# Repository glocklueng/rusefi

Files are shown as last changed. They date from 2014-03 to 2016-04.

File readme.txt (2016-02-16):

current binaries are always available at http://rusefi.com/build_server/

#Releases

| Release date  | Revision  | Details |
| ---  | --- | --- |
| 02/15/2016	| r9600 | automatic warm-up fuel correction, performance improvements
| 08/31/2015	| r8725 | acceleration fuel correction, console improvements
| 07/06/2015	| r8554 | more CAN, better console, bugfixes, performance
| 04/26/2015	| r7938	 | vehicle speed sensor, stepper idle valve, lots of improvements
| 11/13/2014	| r5327	 | ChibiOS/RT 2.6.6, better cold start logic, bugfixes, bugfixes, bugfixes...
| 06/12/2014	| r3477	 | Precise event scheduling, protocol selection 
| 03/26/2014	| r2413	 | C++, refactoring & improvements
| 02/23/2013	| r1777	 | trigger is now configurable via TunerStudio
| 01/30/2014	| r1309	 | true trigger angles, VBatt signal
| 01/12/2014	| r1007	 | refactoring, refactoring & refactoring
| 12/19/2013	| r605	 | ignition control & a little bit of CAN bus
| 11/08/2013	| r100	 | Tuner Studio fuel map tuning, fuel pump control
| 10/14/2013	| r39	 | USB serial bug, missing IAR files, self-containted Makefile
| 10/13/2013	| r33	 | IAR project file
| 10/04/2013	| r26	 | Patched ChibiOS/RT 2.6.1 sources are now included
| 09/23/2013	| r20	 | Tuner Studio integration, configuraton persistence
| 08/30/2013	| r14	 | initial documentation & refactoring. tunerstudio integration
| 08/03/2013	| r13	 | wideband O2 input, better idling algorithm, serial-over-USB
| 07/05/2013	| r10	 | Second CKP, sequential injection.
| 06/19/2013	| r9	 | Initial version - batch injection & ignition with advance table lookup.

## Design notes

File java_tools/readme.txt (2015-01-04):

Here we have some tiny utilities
gcc_map_reader reads the .map file produced by GCC and prints some details on what is RAM used for
ts2c reads a piece of TunerStudio map and produces a matching C language piece of code
version2header creates a C language header containting current SVN version
enum2string

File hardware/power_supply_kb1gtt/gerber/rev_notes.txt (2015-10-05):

This is a copy of https://code.google.com/p/daecu/source/browse/#svn%2FHardware%2Ftrunk%2FKICAD_Project_PWR_buck_12V_switcher with lib split up per standard rusEFI file practices. 

R0.1 first spin
R0.3 adjusted to be easier to MFG with an iron.
R0.4 Added MOSFET that allows 150V surge protection

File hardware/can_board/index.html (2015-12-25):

forum thread (http://rusefi.com/forum/viewtopic.php?f=4&t=353)
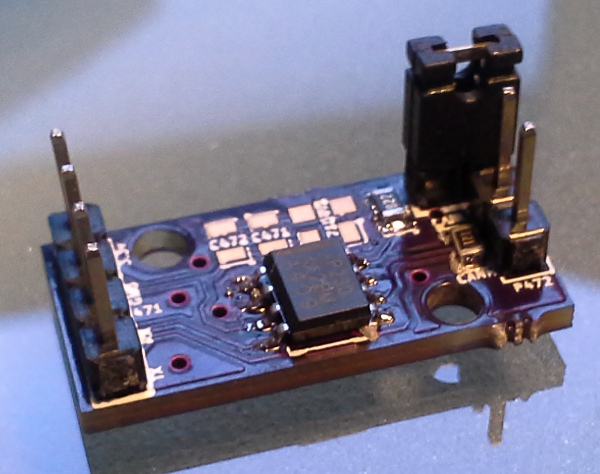
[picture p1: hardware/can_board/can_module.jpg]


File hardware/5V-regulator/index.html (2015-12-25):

forum thread (http://rusefi.com/forum/viewtopic.php?f=4&t=893)
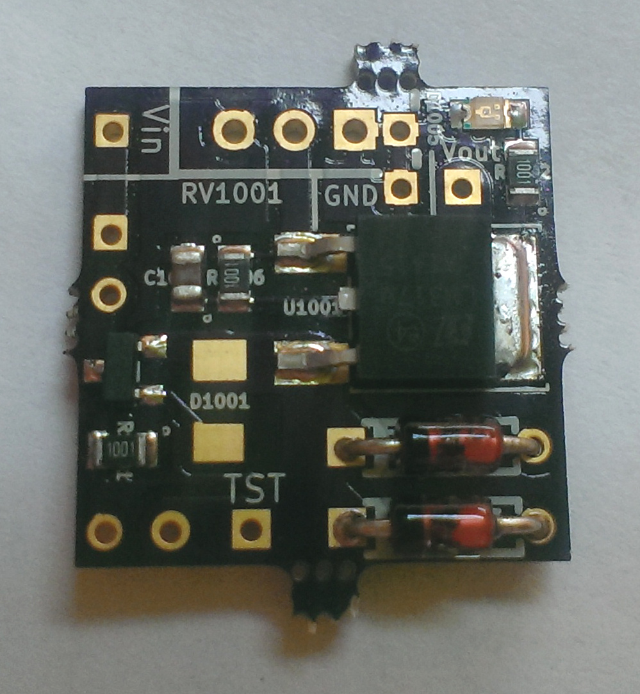
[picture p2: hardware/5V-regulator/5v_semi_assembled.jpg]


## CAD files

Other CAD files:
hardware/mazda_b_case/B3_ECU_PCB.dwg

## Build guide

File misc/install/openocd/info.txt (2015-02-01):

OpenOCD 0.8.0
commit date: 27.04.2014 10:28:21
build date: 28.04.2014
package date: 28.04.2014
build system: Linux 3.14.1-1-ARCH #1 SMP PREEMPT Mon Apr 14 20:40:47 CEST 2014 x86_64 GNU/Linux
compiler: GCC 4.8.2 (i686-w64-mingw32 / x86_64-w64-mingw32; 4.8.2-5 package in Arch Linux)

Libraries used:
hidapi-0.8.0-rc1
libftdi-1.1
libusb-win32-1.2.6.0
libusb-1.0.18

Build commands used for 32-bit version:
../configure --host=i686-w64-mingw32 --prefix= --enable-aice --enable-amtjtagaccel --enable-armjtagew
	--enable-cmsis-dap --enable-ftdi --enable-gw16012 --enable-jlink --enable-jtag_vpi --enable-legacy-ft2232_libftdi
	--enable-opendous --enable-openjtag_ftdi --enable-osbdm --enable-parport --disable-parport-ppdev
	--enable-parport-giveio --enable-presto_libftdi --enable-remote-bitbang --enable-rlink --enable-stlink
	--enable-ti-icdi --enable-ulink --enable-usb-blaster-2 --enable-usb_blaster_libftdi --enable-usbprog
	--enable-vsllink
make bindir="bin" pkgdatadir=
i686-w64-mingw32-strip src/openocd.exe

Build commands used for 64-bit version:
../configure --host=x86_64-w64-mingw32 --prefix= --enable-aice --enable-amtjtagaccel --enable-armjtagew
	--enable-cmsis-dap --enable-ftdi --enable-gw16012 --enable-jlink --enable-jtag_vpi --enable-legacy-ft2232_libftdi
	--enable-opendous --enable-openjtag_ftdi --enable-osbdm --enable-parport --disable-parport-ppdev
	--enable-parport-giveio --enable-presto_libftdi --enable-remote-bitbang --enable-rlink --enable-stlink
	--enable-ti-icdi --enable-ulink --enable-usb-blaster-2 --enable-usb_blaster_libftdi --enable-usbprog
	--enable-vsllink
make bindir="bin-x64" pkgdatadir=
x86_64-w64-mingw32-strip src/openocd.exe

This package and info about it can be found on Freddie Chopin's website:
http://www.freddiechopin.info/

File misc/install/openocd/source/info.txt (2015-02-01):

You can download the source code from sourceforge
http://sourceforge.net/projects/openocd/files/openocd/0.8.0/

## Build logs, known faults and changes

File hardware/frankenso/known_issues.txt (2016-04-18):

 1) RESOLVED IN R0.2  upper mounting hole does not align - see http://rusefi.com/images/Frankenso/frankenso_0_1_back.jpg
 2) RESOLVED IN R0.2  add a jumper to isolate C1002 & C1003 while powered via USB? see http://rusefi.com/forum/viewtopic.php?f=4&t=569&start=50#p9859
 3) RESOLVED IN R0.2  usability issue: GND test pad is under discovery
 4) RESOLVED IN R0.2  add larger +5 test pad?
 5) RESOLVED IN R0.2  add +12 test point?
 6) RESOLVED IN R0.2  Thermocouple needs a via to allow a zip tie to go fully around the connector.
 7) RESOLVED IN R0.2  op-amp reference & part # silkscreen is upside down in relation to the labeling of the actual chips
 8) RESOLVED IN R0.2  Make HIP9011 components into 0805 for common parts
 9) RESOLVED IN R0.2  VDD on STM discovery should be 3V not 5V.  
10) RESOLVED IN R0.2  LCD mounting holes are too small for the Chinese M3 stand-offs
11) RESOLVED IN R0.2  SD card PB4 should be SO not SI PB5 should be SI not SO. 
12) RESOLVED IN R0.2  USB D- and D+ were on wrong pins, D+ now on USB pin 3, TTL RX and TX were also on the wrong pins 
13) RESOLVED IN R0.2  JP212 is to close to the LCD mounting slot.
14) RESOLVED IN R0.4  separate VP lines of our three hi-side mosfers
15) RESOLVED IN R0.2  look into flipping the VR + and - pins
16) RESOLVED IN R0.2  add vias for GND, 12V and 5V for test purposes
17) RESOLVED IN R0.2  add option to GND one side of VR in ECU
18) RESOLVED IN R0.2  HC-OX needs 3.3V not 5V. 
19) RESOLVED IN R0.4  BOM issue: D1001 should be BZT52C7V5-FDICT-ND?
20) RESOLVED IN R0.4  BOM issue: C1001 sch says 470uF but part number is 100uF? CHANGED TO 330uF 35V
21) RESOLVED IN R0.4  SKQUCAA010 is End of Life. I've placed and order to get these in October, but we need a better solution
22) RESOLVED IN R0.2  JP212 should be replaced with JP209 which would be breaking the OUT9 line. That's part of hall-via-op-amp circuirty.  
23) RESOLVED IN R0.4  chip select and such for SPI on thermo-couple chips. 
24) RESOLVED IN R0.4  Change joy stick to ALPS SKRHAAE010 
25) RESOLVED IN R0.2  add a prototype area for future circuits to be tossed in.
26)                   add a couple more low-side chips
27) RESOLVED IN R0.2  surge suppression diode option for some low-side
28) RESOLVED IN R0.2  better silkscreen for P602 & P604 - explicit "5v" "12v" "GND"
29) RESOLVED IN R0.2  Add LED indicators to injector channels. 
30) RESOLVED IN R0.3  3D for C1001 bulk cap has black mark on wrong side
31) RESOLVED IN R0.3  from 1) We've moved the upper mounting hole too far - we need to move it half way back http://rusefi.com/forum/viewtopic.php?f=4&t=735#p12500
32) RESOLVED IN R0.3  C1001 should be 1mm lower to improve clearance with the case
33) RESOLVED IN R0.4  Q411 should be 1.5mm lower to improve clearance with the case (See 47)
34) RESOLVED IN R0.4  Q412 should be moved 3mm to the left, this would probably affect W63 which would affect the whole corner. Maybe move Q412 to the back of the board? (See 47)
35) RESOLVED IN R0.3  rename the recently added low-side diodes and LEDs/resistors into 400 range
36) RESOLVED IN R0.3  test pads explicit silkscreen
37) RESOLVED IN R0.3  test pads on the back of the board
38) RESOLVED IN R0.3  U601/2/3: hard to see pad #1 label on the silkscreen
39) RESOLVED IN R0.3  cap values format inconsistency: C165 is ".1u", C24 C355 C471 C701 are ".1uF" and C104 C211 C291 etc are "0.1uF"
40) RESOLVED IN R0.3  rename JP212 to JP09 since it's sitting on input channel #9
41) RESOLVED IN R0.3  JP211 silkscreen not visible on rev 0.2 (was visible on rev 0.1 before the JP211 move)
42)                   (pedantism) eliminate the 4 unused middle pins on the LCD screen connector
43) RESOLVED IN R0.3  Wxx silkscreen on the back where it's possible - this would help while troubleshooting analog inputs
44) RESOLVED IN R0.3  vertical USB is buggered, vias are to small, ect. 
45) RESOLVED IN R0.3  Move 12V injector flyback diodes to other side of W2
46) RESOLVED IN R0.3  Short out D10.
47) RESOLVED IN R0.4  add vias around ST processor. Orginal board design was a 2 layer, not it's 4 layer. It's better design practice to have GND via's closer to the GND pins.
48) RESOLVED IN R0.3  Per 32) and 33) change W64,63 change to single hole, which allows U chips to move away from enclosre metal wall
49)                   Make hidden text for component values align such that a picture can be caputured that displays the component values. 
50)                   check VR against 1996 Miata's. 
51) RESOLVED IN R0.4  HIP9011 / TPIC8101 CS should be connected some GPIO pin, PB0 would work
52) RESOLVED IN R0.4  CAN_RX line should be connected to PB12, not PD12
53) RESOLVED IN R0.4  Add header for CAN bus with 5V and GND. see P401
54) RESOLVED IN R0.4  verify D9 is the same BOM item as discovery board. D5, D6, D9 CHANGED TO DIGI,497-3707-1-ND ST,BAT60JFILM
55) RESOLVED IN R0.4  Add 5V and GND vias to proto area
56) RESOLVED IN R0.4  Add Top, T-1, T-2 and T-3 to PCB copper layers to more clearly identify layers to MFG
57) RESOLVED IN R0.4  knock2 is actually knock0. Need to fix net names & the pinout picture
58) RESOLVED IN R0.4  Change C166 and C167 to 27pF instead of 20/18pF, to match XTAL specified 20CL. (30*30)/(30+30)+5= 20pF with 5pF stray capacitance.
59) RESOLVED IN R0.4  add pF cap to HIP9011 / TPIC8101 knock chip to help fast transients and XTAL starting.
60) RESOLVED IN R0.4  FIX CLAIMED ERRORS IN SCHEMATIC ERC power flags added to resolve 
61) RESOLVED IN R0.4  remove AC RELAY ect from harness connector net names.
62) RESOLVED IN R0.4  add 0R jumper between 5V and 5V plane to allow power supply verification before powering the 5V devices. 
63)                   add resistor divider or some mechanism for identifying via firmware sensing PCB revision. Perhaps to PB1 AN input 
64) RESOLVED IN R0.4  better test pads silkscreen: 5V, GND, 12V
65) RESOLVED IN R0.4  LED for cam/crank signal. we can remove cam/crank test points if we need space GOING TO BE DIM, AS IT NEED 10K SERIES RESISTOR
66) RESOLVED IN R0.4  why do we have W1002 & W1003 if these are usually there? Removing them would remove one point of failure SEE 78)
67)                   JP04 & JP05 are defined on the main schematics sheet. It would be better to define then on Page 8 with the rest of cam/crank stuff
68) RESOLVED IN R0.4  Updated silk screen notes, draws .12 amps normal, with a typical inrush of .3A. 
69) RESOLVED IN R0.4  Look into LCD dimming R99, perhaps replace with a POT. Perhaps connect to a GPIO
70) RESOLVED IN R0.5 Clamp input voltage, as of R0.4 a surge will likely blow an upstream fuse. FIXED, ADDED Q1003 AND FRIENDS
71) RESOLVED IN R0.4  Some USB connectors are wider and hit the PCB making it hard to insert. MOVED PCB EDGE TO BE CLOSER TO USB CONNECTOR.
72) RESOLVED IN R0.4  TI TPIC8101 part number instead of HIP9011
73) RESOLVED IN R0.4  more holes for proto
74)                   one of LCD holes the traces are too close on the back FIXED BUT NEED TO VERIFY FOR REAL WITH BOARD SPIN.
75) RESOLVED IN R0.4  order new joystick for paper test
76) RESOLVED IN R0.4  HIP9011 / TPIC8101 chip has a problem with starting, RESOLVED BY ADDING CAP BETWEEN CS AND XIN TO CREATE STARTING PING. 
77) RESOLVED IN R0.4  AN inputs are limited to operation between 0V and 4V.RESOLVED BY CHANGING OP-AMP TO A BETTER RAIL TO RAIL THAT IS MUCH CLOSER TO THE RAIL.
78) RESOLVED IN R0.4  W1002 - silksceen on the wrong place
79) RESOLVED IN R0.4  1K and 0R on the MAX9926 input: need to put a comment on the schematics page explaining that none or just one of them should be installed depending on the use-case SEE 65)
80) RESOLVED IN R0.4  on schematics, rename INJ_xx to LOW_xx? "inj" is a bit confusing, it implies that PE6 is injector #1 while it is usually not the case
81) RESOLVED IN R0.4  set analog input values to match https://docs.google.com/spreadsheets/d/1LTvS7I-128Hft9uXHG1JrBxetVjGJDSBkySgVDQ6MGk/edit#gid=0
82) RESOLVED IN R0.4  remove 'REAR-DEFROSTER-SW' and etc from schematics
83) RESOLVED IN R0.4  Add silk screen note that fire extinguisher is minimal required equipment. 
84)                   Add baro sensor. 
85)                   add humidity sensor perhaps HIH6120-021-001 or DHT11
86) RESOLVED IN R0.4  Add 2 more hi/low drivers re-used 2x IO from unused joystick leads. Joystick leads are jumper connected to PD0 and PD2
87) RESOLVED IN R0.4  Move low side 7 to PD3, and low side 10 to PD5 (removes yellow and blue jumper wires)
88) RESOLVED IN R0.4.1 R167 and R168 should be 0805 not 1206 CORRECTED TO 0805
89) RESOLVED IN R0.4.1 1K parts call for 100k part, CORRECTED TO 1K
90) RESOLVED IN R0.4.1 C103 should be 0805 current part calls for 1206 CORRECTED TO 0805
91) RESOLVED IN R0.4.1 Can we use 1oz internal layers ADDED MIN NOTE TO THE PCB FILE WHICH ALLOWS THICKER CU. 
92) RESOLVED IN R0.4.1 L1001 and L1002 "ref" part is confusing ADDED SOME NOTES TO CLARIFY TO USE THE SKYMACAU PART
93)                    added pololu stepper driver Perhaps should be an add-on board. 
94) RESOLVED IN R0.4.2 C701, LD601, LD602, LD605, LD606 silk screen mangled. 
95) RESOLVED IN R0.4.2 D1001 doesn't have a polarity indicator in the silk screen
96)                   route unused stm32 pins (D3 PC13 etc) to unused connector pins
97)                   cheaper battery holder - through-hole (need to find out footprint)
98)                   idle valve SMD diode?
99)                   silkscreen for analog inputs - PA1/PC1/etc?
100)                   Swap brain board for 176 pin brain board. 
101) RESOLVED IN R0.5 update TPIC chip for 39k's, 3.3nF, and DNP 1M. 
102)                  connector middle mounting holes - need a 5.5mm diameter area for screw head on the back
103) RESOLVED IN R0.5 TPIC/HIP knock SPI was not working properly, R170 changed to 5k and R172 to R174 removed to correct the SPI bus. 
104) RESOLVED IN R0.5 U5 button silkscreen notch is barely visible
105) RESOLVED IN R0.5 D161 TPIC8101 silk screen is a bit messed up. 
106) RESOLVED IN R0.5 Change X161 to same 8MHz X1.
107)                  Per this PDF http://www.ti.com/lit/an/snva538/snva538.pdf the switch mode power supply may have some EMC noise issues. 
108) RESOLVED IN R0.5 Q1001 was Alpha,AO3401A and changed to Vishay SQ2301ES-T1-GE3 which is automotive AEC-Q101 qualified. 
109)                  Move D12-D23 schematics from the main page to the inj12ch page
110)                  Part number for D19 (PB9-INJ09/PB9) as Miata Idle Valve Solenoid
111)                  GND and +12v rails? at least some 1.1mm holes in the prototyping area. Make holes larger for larger wires.
112)                  reduce high-side schematics confusion where H_IN1 is HL2, H_IN3 is HL1 etc.see http://rusefi.com/forum/viewtopic.php?f=4&t=569&start=240
113) RESOLVED IN R0.5 "Normal + Insert" attributes for all SIL-2 and SOD-123 footprints to fix position file generation

For honda add-on / rewiring board
-- Add 2A high side solinoid drive for VTec sol
-- Add 3rd VR chip for 3rd signal
-- Add selectable high side drive with +5V or +12V options
-- re-wire to allow freindly pinout

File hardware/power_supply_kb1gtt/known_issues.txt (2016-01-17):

This is a copy of https://code.google.com/p/daecu/source/browse/#svn%2FHardware%2Ftrunk%2FKICAD_Project_PWR_buck_12V_switcher with lib split up per standard rusEFI file practices. 

V.2 of this board was MFG'ed, and assembled. 
It functioned with out modifications. 
Mild changes were made to R.03 making it easier to assembly via iron soldering. 
As of 06/14/14, validation is still being done.

V0.4 added high voltage mostfet which allows 150V surges with out damageing the down stream components. 
V0.4 Made KICAD 4.01 compatable
V0.4 Added L3 RF choke.

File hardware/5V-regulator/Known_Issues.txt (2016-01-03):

1) RESOLVED IN R0.2 Add polarity indicator silk screen to D1001
2) RESOLVED IN R0.2 Add reverse diode D1 noted http://datasheet.octopart.com/LM317MDTG-ON-Semiconductor-datasheet-512589.pdf ADDED D1004
3) RESOLVED IN R0.2 Change symbol for D1003

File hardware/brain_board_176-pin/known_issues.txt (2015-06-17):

1)                  on the back, battery holder overlaps five caps and one resistor
2) RESOLVED IN R0.2 FB1 BOM missing.
3) RESOLVED IN R0.2 BYPASS_REG to GND
4) RESOLVED IN R0.2 back side silkscreen does not match front side silkscreen (multiple instances)
5) RESOLVED IN R0.2 X2 pinout what is connected to pin 2, should be connected to pin 4.

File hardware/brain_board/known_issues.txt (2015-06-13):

1)                  PA9 <> USB VBUS trace is needed to get USB functional

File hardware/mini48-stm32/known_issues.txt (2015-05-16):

		PA13 mention SWDIO in schematics, PA14 mention SWCLK
		pins PB14 & PB15: wrong silkscreen

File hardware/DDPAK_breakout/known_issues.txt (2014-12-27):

1) RESOLVED IN R0.2 DPAK2 is apparently different than D2PAK, now it uses TO-263AB
2) RESOLVED IN R0.2 Make vias under large GND pad larger to allow more heat form iron during soldering
3) RESOLVED IN R0.2 move Via's to PCB edge to allow install on proto area of Frankenso
4) RESOLVED IN R0.2 add 4-40 mounting screw hole(s)

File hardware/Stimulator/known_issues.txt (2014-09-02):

1) changed in R0.2 -- silkscreen font is really small
2) changed in R0.2 -- add breakout holes for all unused pins to simplify CS routing
3) changed in R0.2 -- add 'Power' LED
4) changed in R0.2 -- add two MAX232 chips (four VR stimulation channels)
5) changed in R0.2 -- merge 5v's
6) changed in R0.2 -- add ECU power LED
7) todo:              reduce width to 10cm/3.93701 inches

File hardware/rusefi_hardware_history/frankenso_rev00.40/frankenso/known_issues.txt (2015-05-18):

 1) RESOLVED IN R0.2 upper mounting hole does not align - see http://rusefi.com/images/Frankenso/frankenso_0_1_back.jpg
 2) RESOLVED IN R0.2 add a jumper to isolate C1002 & C1003 while powered via USB? see http://rusefi.com/forum/viewtopic.php?f=4&t=569&start=50#p9859
 3) RESOLVED IN R0.2 usability issue: GND test pad is under discovery
 4) RESOLVED IN R0.2 add larger +5 test pad?
 5) RESOLVED IN R0.2 add +12 test point?
 6) RESOLVED IN R0.2 Thermocouple needs a via to allow a zip tie to go fully around the connector.
 7) RESOLVED IN R0.2 op-amp reference & part # silkscreen is upside down in relation to the labeling of the actual chips
 8) RESOLVED IN R0.2 Make HIP9011 components into 0805 for common parts
 9) RESOLVED IN R0.2 VDD on STM discovery should be 3V not 5V.  
10) RESOLVED IN R0.2 LCD mounting holes are too small for the Chinese M3 stand-offs
11) RESOLVED IN R0.2 SD card PB4 should be SO not SI PB5 should be SI not SO. 
12) RESOLVED IN R0.2 USB D- and D+ were on wrong pins, D+ now on USB pin 3, TTL RX and TX were also on the wrong pins 
13) RESOLVED IN R0.2 JP212 is to close to the LCD mounting slot.
14) RESOLVED IN R0.4 separate VP lines of our three hi-side mosfers
15) RESOLVED IN R0.2 look into flipping the VR + and - pins
16) RESOLVED IN R0.2 add vias for GND, 12V and 5V for test purposes
17) RESOLVED IN R0.2 add option to GND one side of VR in ECU
18) RESOLVED IN R0.2 HC-OX needs 3.3V not 5V. 
19) RESOLVED IN R0.4 BOM issue: D1001 should be BZT52C7V5-FDICT-ND?
20) RESOLVED IN R0.4 BOM issue: C1001 sch says 470uF but part number is 100uF? CHANGED TO 330uF 35V
21) RESOLVED IN R0.4 SKQUCAA010 is End of Life. I've placed and order to get these in October, but we need a better solution
22) RESOLVED IN R0.2 JP212 should be replaced with JP209 which would be breaking the OUT9 line. That's part of hall-via-op-amp circuirty.  
23) RESOLVED IN R0.4 chip select and such for SPI on thermo-couple chips. 
24) RESOLVED IN R0.4 Change joy stick to ALPS SKRHAAE010 
25) RESOLVED IN R0.2 add a prototype area for future circuits to be tossed in.
26)                  add a couple more low-side chips
27) RESOLVED IN R0.2 surge suppression diode option for some low-side
28) RESOLVED IN R0.2 better silkscreen for P602 & P604 - explicit "5v" "12v" "GND"
29) RESOLVED IN R0.2 Add LED indicators to injector channels. 
30) RESOLVED IN R0.3 3D for C1001 bulk cap has black mark on wrong side
31) RESOLVED IN R0.3 from 1) We've moved the upper mounting hole too far - we need to move it half way back http://rusefi.com/forum/viewtopic.php?f=4&t=735#p12500
32) RESOLVED IN R0.3 C1001 should be 1mm lower to improve clearance with the case
32) RESOLVED IN R0.4 Q411 should be 1.5mm lower to improve clearance with the case (See 47)
33) RESOLVED IN R0.4 Q412 should be moved 3mm to the left, this would probably affect W63 which would affect the whole corner. Maybe move Q412 to the back of the board? (See 47)
34) RESOLVED IN R0.3 rename the recently added low-side diodes and LEDs/resistors into 400 range
35) RESOLVED IN R0.3 test pads explicit silkscreen
36) RESOLVED IN R0.3 test pads on the back of the board
37) RESOLVED IN R0.3 U601/2/3: hard to see pad #1 label on the silkscreen
38) RESOLVED IN R0.3 cap values format inconsistency: C165 is ".1u", C24 C355 C471 C701 are ".1uF" and C104 C211 C291 etc are "0.1uF"
39) RESOLVED IN R0.3 rename JP212 to JP09 since it's sitting on input channel #9
40) RESOLVED IN R0.3 JP211 silkscreen not visible on rev 0.2 (was visible on rev 0.1 before the JP211 move)
41)                  (pedantism) eliminate the 4 unused middle pins on the LCD screen connector
42) RESOLVED IN R0.3 Wxx silkscreen on the back where it's possible - this would help while troubleshooting analog inputs
43) RESOLVED IN R0.3 vertical USB is buggered, vias are to small, ect. 
44) RESOLVED IN R0.3 Move 12V injector flyback diodes to other side of W2
45) RESOLVED IN R0.3 Short out D10.
46) RESOLVED IN R0.4 add vias around ST processor. Orginal board design was a 2 layer, not it's 4 layer. It's better design practice to have GND via's closer to the GND pins.
47) RESOLVED IN R0.3 Per 32) and 33) change W64,63 change to single hole, which allows U chips to move away from enclosre metal wall
48)                  Make hidden text for component values align such that a picture can be caputured that displays the component values. 
49)                  check VR against 1996 Miata's. 
50) RESOLVED IN R0.4 HIP9011 / TPIC8101 CS should be connected some GPIO pin, PB0 would work
51) RESOLVED IN R0.4 CAN_RX line should be connected to PB12, not PD12
52) RESOLVED IN R0.4 Add header for CAN bus with 5V and GND. see P401
53) RESOLVED IN R0.4 verify D9 is the same BOM item as discovery board. D5, D6, D9 CHANGED TO DIGI,497-3707-1-ND ST,BAT60JFILM
54) RESOLVED IN R0.4 Add 5V and GND vias to proto area
55) RESOLVED IN R0.4 Add Top, T-1, T-2 and T-3 to PCB copper layers to more clearly identify layers to MFG
56) RESOLVED IN R0.4 knock2 is actually knock0. Need to fix net names & the pinout picture
57) RESOLVED IN R0.4 Change C166 and C167 to 27pF instead of 20/18pF, to match XTAL specified 20CL. (30*30)/(30+30)+5= 20pF with 5pF stray capacitance.
58) RESOLVED IN R0.4 add pF cap to HIP9011 / TPIC8101 knock chip to help fast transients and XTAL starting.
59) RESOLVED IN R0.4 FIX CLAIMED ERRORS IN SCHEMATIC ERC power flags added to resolve 
60) RESOLVED IN R0.4 remove AC RELAY ect from harness connector net names.
61) RESOLVED IN R0.4 add 0R jumper between 5V and 5V plane to allow power supply verification before powering the 5V devices. 
62)                  add resistor divider or some mechanism for identifying via firmware sensing PCB revision. Perhaps to PB1 AN input 
63) RESOLVED IN R0.4 better test pads silkscreen: 5V, GND, 12V
64) RESOLVED IN R0.4 LED for cam/crank signal. we can remove cam/crank test points if we need space GOING TO BE DIM, AS IT NEED 10K SERIES RESISTOR
65) RESOLVED IN R0.4 why do we have W1002 & W1003 if these are usually there? Removing them would remove one point of failure SEE 78)
66)                  JP04 & JP05 are defined on the main schematics sheet. It would be better to define then on Page 8 with the rest of cam/crank stuff
67) RESOLVED IN R0.4 Updated silk screen notes, draws .12 amps normal, with a typical inrush of .3A. 
68) RESOLVED IN R0.4 Look into LCD dimming R99, perhaps replace with a POT. Perhaps connect to a GPIO
69)                  Change F1 to a wire wound resistor which will also be the weak link and act like a fuse before the PCB breaks, while also snubbing RF
70) RESOLVED IN R0.4 Some USB connectors are wider and hit the PCB making it hard to insert. MOVED PCB EDGE TO BE CLOSER TO USB CONNECTOR.
71) RESOLVED IN R0.4 TI TPIC8101 part number instead of HIP9011
72) RESOLVED IN R0.4 more holes for proto
73)                  one of LCD holes the traces are too close on the back FIXED BUT NEED TO VERIFY FOR REAL WITH BOARD SPIN.
74) RESOLVED IN R0.4 order new joystick for paper test
75) RESOLVED IN R0.4 HIP9011 / TPIC8101 chip has a problem with starting, RESOLVED BY ADDING CAP BETWEEN CS AND XIN TO CREATE STARTING PING. 
76) RESOLVED IN R0.4 AN inputs are limited to operation between 0V and 4V.RESOLVED BY CHANGING OP-AMP TO A BETTER RAIL TO RAIL THAT IS MUCH CLOSER TO THE RAIL.
77) RESOLVED IN R0.4 W1002 - silksceen on the wrong place
78) RESOLVED IN R0.4 1K and 0R on the MAX9926 input: need to put a comment on the schematics page explaining that none or just one of them should be installed depending on the use-case SEE 65)
79) RESOLVED IN R0.4 on schematics, rename INJ_xx to LOW_xx? "inj" is a bit confusing, it implies that PE6 is injector #1 while it is usually not the case
80) RESOLVED IN R0.4 set analog input values to match https://docs.google.com/spreadsheets/d/1LTvS7I-128Hft9uXHG1JrBxetVjGJDSBkySgVDQ6MGk/edit#gid=0
81) RESOLVED IN R0.4 remove 'REAR-DEFROSTER-SW' and etc from schematics
82) RESOLVED IN R0.4 Add silk screen note that fire extinguisher is minimal required equipment. 
83)                  Add baro sensor. 
84)                  add humidity sensor perhaps HIH6120-021-001 or DHT11
85) RESOLVED IN R0.4 Add 2 more hi/low drivers re-used 2x IO from unused joystick leads. Joystick leads are jumper connected to PD0 and PD2
86) RESOLVED IN R0.4 Move low side 7 to PD3, and low side 10 to PD5 (removes yellow and blue jumper wires)

For honda add-on / rewiring board
-- Add 2A high side solinoid drive for VTec sol
-- Add 3rd VR chip for 3rd signal
-- Add selectable high side drive with +5V or +12V options
-- re-wire to allow freindly pinout

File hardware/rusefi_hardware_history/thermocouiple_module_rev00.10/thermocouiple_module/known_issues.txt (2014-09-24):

 1) resolved in R0.2 SPI silk screen is not correct.
 2)                  5.04 screw-in terminal option
 3)                  multichannel?

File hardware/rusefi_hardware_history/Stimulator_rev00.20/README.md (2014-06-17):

Stimulator
==========

Rusefi Stimulator

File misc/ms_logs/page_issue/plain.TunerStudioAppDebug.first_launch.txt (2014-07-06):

TunerStudio 2.6.01 started on Sat Jul 05 20:55:36 EDT 2014
JRE 1.7.0_60, Windows 7 6.1, x86
java.library.path=lib
TunerStudioMS.jar
Look:Metal, ClassName:'javax.swing.plaf.metal.MetalLookAndFeel'
Look:Nimbus, ClassName:'javax.swing.plaf.nimbus.NimbusLookAndFeel'
Look:CDE/Motif, ClassName:'com.sun.java.swing.plaf.motif.MotifLookAndFeel'
Look:Windows, ClassName:'com.sun.java.swing.plaf.windows.WindowsLookAndFeel'
Look:Windows Classic, ClassName:'com.sun.java.swing.plaf.windows.WindowsClassicLookAndFeel'
Setting Look & Feel to:javax.swing.plaf.metal.MetalLookAndFeel
7/5/14 8:55:37 PM :Debug: Command Non-VolatileBytes for F resolved to: x46                                                                   F
7/5/14 8:55:37 PM :Debug: Command Non-VolatileBytes for I resolved to: x49                                                                   I
7/5/14 8:55:37 PM :Debug: Command Non-VolatileBytes for f resolved to: x66                                                                   f
7/5/14 8:55:37 PM :Debug: App Name:TunerStudio, appEdition:MS Lite!
7/5/14 8:55:39 PM :Debug: Time to retreive font name list: 32 ms.
WARNING:  RXTX Version mismatch
	Jar version = RXTX-2.2pre1
	native lib Version = RXTX-2.1-7
7/5/14 8:55:39 PM :Info: Initialized RXTX driver: 10ms.
No check, last update check=Fri Jul 04 15:49:57 EDT 2014
MSmain: No check, last update check=Fri Jul 04 15:49:54 EDT 2014
MSad: No check, last update check=Fri Jul 04 15:49:57 EDT 2014
7/5/14 8:55:51 PM :Debug: Time to load ini list: 10ms.
7/5/14 8:55:59 PM :Debug: Filtered ConfigurationOptionGroup in 2ms.
7/5/14 8:56:00 PM :Info: Read file canPcVariables.ini: 0.0ms
7/5/14 8:56:00 PM :Info: Filtered ini: 0.0ms
7/5/14 8:56:00 PM :Info: Loading Trigger Wheels
7/5/14 8:56:00 PM :Info: Loaded All known ini sections
7/5/14 8:56:00 PM :Info: Parsed and validated ini "canPcVariables.ini" in : 33ms.
7/5/14 8:56:00 PM :Info: Read file rusefi.ini: 1.0ms
7/5/14 8:56:00 PM :Info: Filtered ini: 0.0ms
7/5/14 8:56:00 PM :Debug: ini signature: MShift v0.01
7/5/14 8:56:00 PM :Info: Set Write Blocks on = true
7/5/14 8:56:00 PM :Info: Loading Trigger Wheels
7/5/14 8:56:00 PM :Info: Loaded All known ini sections
7/5/14 8:56:00 PM :Info: Parsed and validated ini "rusefi.ini" in : 25ms.
7/5/14 8:56:00 PM :Debug: Adding Configuration: MyCar
7/5/14 8:56:00 PM :Info: No secl OutputChannel, och sync monitor disabled.
7/5/14 8:56:02 PM :Debug: goOffline Starting, Time:0
7/5/14 8:56:02 PM :Info: Deactivated Turbo Baud, goOffline
7/5/14 8:56:02 PM :Debug: goOffline about to stopProcessing, Time:1
7/5/14 8:56:02 PM :Debug: currentPort == null:true
7/5/14 8:56:02 PM :Debug: goOffline closed port, Time:1
7/5/14 8:56:02 PM :Debug: goOffline comm thread stopped, Time:1
7/5/14 8:56:02 PM :Debug: No Remaining Queue Write instructions
7/5/14 8:56:02 PM :Debug: removing Configuration: MyCar
7/5/14 8:56:02 PM :Info: No Persistor set, not saving active triggers.
7/5/14 8:56:02 PM :Debug: Cancel Wizard
7/5/14 8:56:14 PM :Debug: Time to load ini list: 12ms.
7/5/14 8:56:22 PM :Debug: Filtered ConfigurationOptionGroup in 1ms.
7/5/14 8:56:23 PM :Info: Read file canPcVariables.ini: 0.0ms
7/5/14 8:56:23 PM :Info: Filtered ini: 0.0ms
7/5/14 8:56:23 PM :Info: Loading Trigger Wheels
7/5/14 8:56:23 PM :Info: Loaded All known ini sections
7/5/14 8:56:23 PM :Info: Parsed and validated ini "canPcVariables.ini" in : 2ms.
7/5/14 8:56:23 PM :Info: Read file rusefi.ini: 26.0ms
7/5/14 8:56:23 PM :Info: Filtered ini: 0.0ms
7/5/14 8:56:23 PM :Debug: ini signature: MShift v0.01
7/5/14 8:56:23 PM :Info: Set Write Blocks on = true
7/5/14 8:56:23 PM :Info: Loading Trigger Wheels
7/5/14 8:56:23 PM :Info: Loaded All known ini sections
7/5/14 8:56:23 PM :Info: Parsed and validated ini "rusefi.ini" in : 39ms.
7/5/14 8:56:23 PM :Debug: Adding Configuration: MyCar
7/5/14 8:56:23 PM :Info: No secl OutputChannel, och sync monitor disabled.
7/5/14 8:56:27 PM :Debug: Time to save Dash: 55 ms.
7/5/14 8:56:27 PM :Debug: High Speed Paint: true
7/5/14 8:56:27 PM :Debug: High Speed Paint: true
7/5/14 8:56:28 PM :Warning: Could not get Firmware signature
7/5/14 8:56:28 PM :Debug: Time to save Dash: 15 ms.
7/5/14 8:56:28 PM :Debug: goOffline Starting, Time:0
7/5/14 8:56:28 PM :Info: Deactivated Turbo Baud, goOffline
7/5/14 8:56:28 PM :Debug: goOffline about to stopProcessing, Time:0
7/5/14 8:56:28 PM :Debug: currentPort == null:true
7/5/14 8:56:28 PM :Debug: goOffline closed port, Time:0
7/5/14 8:56:28 PM :Debug: goOffline comm thread stopped, Time:0
7/5/14 8:56:28 PM :Debug: No Remaining Queue Write instructions
7/5/14 8:56:28 PM :Debug: goOffline Starting, Time:0
7/5/14 8:56:28 PM :Info: Deactivated Turbo Baud, goOffline
7/5/14 8:56:28 PM :Debug: goOffline about to stopProcessing, Time:0
7/5/14 8:56:28 PM :Debug: currentPort == null:true
7/5/14 8:56:28 PM :Debug: goOffline closed port, Time:0
7/5/14 8:56:28 PM :Debug: goOffline comm thread stopped, Time:0
7/5/14 8:56:28 PM :Debug: No Remaining Queue Write instructions
7/5/14 8:56:28 PM :Debug: removing Configuration: MyCar
7/5/14 8:56:28 PM :Info: No Persistor set, not saving active triggers.
7/5/14 8:56:28 PM :Debug: Opening project: C:\Users\pc\Documents\TunerStudioProjects\MyCar
7/5/14 8:56:28 PM :Debug: Reading translation file as plain text because: fast binary headers not found. probably not a fast binary file
7/5/14 8:56:28 PM :Debug: Filtered ConfigurationOptionGroup in 1ms.
7/5/14 8:56:28 PM :Info: Read file canPcVariables.ini: 0.0ms
7/5/14 8:56:28 PM :Info: Filtered ini: 0.0ms
7/5/14 8:56:28 PM :Info: Loading Trigger Wheels
7/5/14 8:56:28 PM :Info: Loaded All known ini sections
7/5/14 8:56:28 PM :Info: Parsed and validated ini "canPcVariables.ini" in : 3ms.
7/5/14 8:56:28 PM :Info: Read file mainController.ini: 1.0ms
7/5/14 8:56:28 PM :Info: Filtered ini: 0.0ms
7/5/14 8:56:28 PM :Debug: ini signature: MShift v0.01
7/5/14 8:56:28 PM :Info: Set Write Blocks on = true
7/5/14 8:56:28 PM :Info: Loading Trigger Wheels
7/5/14 8:56:28 PM :Info: Loaded All known ini sections
7/5/14 8:56:28 PM :Info: Parsed and validated ini "mainController.ini" in : 9ms.
7/5/14 8:56:28 PM :Info: Not Loading default Tools because non are defined for signature: MShift v0.01
7/5/14 8:56:28 PM :Debug: Adding Configuration: MyCar
7/5/14 8:56:28 PM :Info: No secl OutputChannel, och sync monitor disabled.
7/5/14 8:56:28 PM :Info: !!! Loaded config in 71
7/5/14 8:56:28 PM :Info: Opening port: COM18
7/5/14 8:56:28 PM :Debug: 0ms. - added Port
7/5/14 8:56:28 PM :Debug: 28ms. - 1st got port
7/5/14 8:56:28 PM :Debug: 28ms. - got port
7/5/14 8:56:28 PM :Debug: 35ms. - setParameters
7/5/14 8:56:28 PM :Debug: Monitoring COM18 @ 115200 baud for controllers.
7/5/14 8:56:28 PM :Debug: Started new CommThread for MyCar
7/5/14 8:56:28 PM :Info: Comm Manager for MyCar Started
7/5/14 8:56:28 PM :Debug: commThreadExpectedReturnTime set to ms from now: 1220
7/5/14 8:56:28 PM :Debug: Comm Read Thread Change! Old Thread:null, new Thread:COMM Thread13625.093399768062
7/5/14 8:56:28 PM :Info: Started Comms Watchdog
7/5/14 8:56:28 PM :Info: !!! Activated Project 145
7/5/14 8:56:28 PM :Time: 0:00.091: SENT, 1 bytes
x46                                                                   F

7/5/14 8:56:28 PM :Debug: High Speed Paint: true
7/5/14 8:56:28 PM :Debug: !!! Opened Dash 236
7/5/14 8:56:29 PM :Debug: commThreadExpectedReturnTime set to ms from now: 1620
7/5/14 8:56:29 PM :Time: 0:00.691: Received, 3 bytes
x30 x30 x31                                                           001

7/5/14 8:56:29 PM :Time: 0:00.691: SENT, 1 bytes
x48                                                                   H

7/5/14 8:56:29 PM :Info: Communicating with Bowling & Grippo MS1 Base Code MShift v0.01
7/5/14 8:56:29 PM :Time: 0:01.492: Received, 13 bytes
x4D x53 x68 x69 x66 x74 x20 x76 x30 x2E x30 x31 x00                   MShift.v0.01.

Time: 0:01.493: Received Instruction: 
Time: 0:01.537: Processing Instruction: 
7/5/14 8:56:29 PM :Debug: Reading ECU Data, 0.0 complete
7/5/14 8:56:29 PM :Debug: commThreadExpectedReturnTime set to ms from now: 860
7/5/14 8:56:29 PM :Time: 0:01.595: SENT, 3 bytes
x50 x00 x00                                                           P..

7/5/14 8:56:30 PM :Debug: commThreadExpectedReturnTime set to ms from now: 20140
7/5/14 8:56:30 PM :Time: 0:01.705: SENT, 7 bytes
x52 x00 x00 x00 x00 x64 x05                                           R....d.

7/5/14 8:56:30 PM :Debug: Read page time: 210ms.
7/5/14 8:56:30 PM :Debug: Reading ECU Data, 0.25 complete
7/5/14 8:56:30 PM :Time: 0:01.856: Received, 1380 bytes
x00 x00 x00 x00 x9A x99 xEF x42 x00 x00 x00 x41 x00 x00 x10 x41       .......B...A...A
x00 x00 x20 x41 x00 x00 x30 x41 x00 x00 x40 x41 x00 x00 x50 x41       ...A..0A..@A..PA
x00 x00 x60 x41 x00 x00 x70 x41 x00 x00 x00 x00 x00 x00 x00 x00       ..`A..pA........
x00 x00 x00 x00 x00 x00 x00 x00 x00 x00 x00 x00 x00 x00 x00 x00       ................
x00 x00 x00 x00 x00 x00 x00 x00 x00 x00 x20 xC2 x00 x00 xF0 xC1       ................
x00 x00 xA0 xC1 x00 x00 x20 xC1 x00 x00 x00 x00 x00 x00 x20 x41       ...............A
x00 x00 xA0 x41 x00 x00 xF0 x41 x00 x00 x20 x42 x00 x00 x48 x42       ...A...A...B..HB
x00 x00 x70 x42 x00 x00 x8C x42 x00 x00 xA0 x42 x00 x00 xB4 x42       ..pB...B...B...B
x00 x00 xC8 x42 x00 x00 xDC x42 x00 x00 x80 x3F x00 x00 x80 x3F       ...B...B...?...?
x00 x00 x80 x3F x00 x00 x80 x3F x00 x00 x80 x3F x00 x00 x80 x3F       ...?...?...?...?
x00 x00 x80 x3F x00 x00 x80 x3F x00 x00 x80 x3F x00 x00 x80 x3F       ...?...?...?...?
x00 x00 x80 x3F x00 x00 x80 x3F x00 x00 x80 x3F x00 x00 x80 x3F       ...?...?...?...?
x00 x00 x80 x3F x00 x00 x80 x3F x00 x00 x20 xC2 x00 x00 xF0 xC1       ...?...?........
x00 x00 xA0 xC1 x00 x00 x20 xC1 x00 x00 x00 x00 x00 x00 x20 x41       ...............A
x00 x00 xA0 x41 x00 x00 xF0 x41 x00 x00 x20 x42 x00 x00 x48 x42       ...A...A...B..HB
x00 x00 x70 x42 x00 x00 x8C x42 x00 x00 xA0 x42 x00 x00 xB4 x42       ..pB...B...B...B
x00 x00 xC8 x42 x00 x00 xDC x42 x00 x00 x80 x3F x00 x00 x80 x3F       ...B...B...?...?
x00 x00 x80 x3F x00 x00 x80 x3F x00 x00 x80 x3F x00 x00 x80 x3F       ...?...?...?...?
x00 x00 x80 x3F x00 x00 x80 x3F x00 x00 x80 x3F x00 x00 x80 x3F       ...?...?...?...?
x00 x00 x80 x3F x00 x00 x80 x3F x00 x00 x80 x3F x00 x00 x80 x3F       ...?...?...?...?
x00 x00 x80 x3F x00 x00 x80 x3F x00 x00 x64 x00 xEE x02 x01 x00       ...?...?..d.....
x00 x00 x00 x00 x00 x00 x82 x42 x00 x00 x70 x41 x00 x00 x00 x41       .......B..pA...A
x26 x02 x00 x00 x00 x00 x48 x44 xB8 xB6 xD2 x44 xB8 xB6 x20 x45       &.....HD...D...E
x3D x12 x58 x45 xCD xB6 x87 x45 x8F x64 xA3 x45 x3D x12 xBF x45       =.XE...E.d.E=..E
x00 xC0 xDA x45 x00 x00 x00 x00 x00 x00 x00 x00 x00 x00 x00 x00       ...E............
x00 x00 x00 x00 x00 x00 x00 x00 x00 x00 x00 x00 x00 x00 x00 x00       ................
x00 x00 x00 x00 x00 x00 x48 x44 xB8 xB6 xD2 x44 xB8 xB6 x20 x45       ......HD...D...E
x3D x12 x58 x45 xCD xB6 x87 x45 x8F x64 xA3 x45 x3D x12 xBF x45       =.XE...E.d.E=..E
x00 xC0 xDA x45 x00 x00 x00 x00 x00 x00 x00 x00 x00 x00 x00 x00       ...E............
x00 x00 x00 x00 x00 x00 x00 x00 x00 x00 x00 x00 x00 x00 x00 x00       ................
x00 x00 x00 x00 x00 x00 x00 x00 x00 x00 x00 x00 x01 x00 x00 x00       ................
x04 x00 x00 x00 x00 x00 xA0 xC1 x78 x1C xBF x41 x3C x8E x43 x42       ........x..A<.CB
x00 xA0 x8C x46 x00 x40 x03 x45 x00 x00 x7A x44 x00 x40 x4E x45       ...F.@.E..zD.@NE
x40 xB6 x5A xB9 x08 x13 x0C x3A x8C xA2 x99 xB5 x00 x00 x00 x42       @.Z....:.......B
x00 x00 x96 x42 x00 x00 xF0 x42 x00 x70 x14 x46 x00 x40 x03 x45       ...B...B.p.F.@.E
x00 x00 x7A x44 x00 xC0 x28 x45 x76 x1A x47 xBB xB4 xCE x7C x3A       ..zD..(Ev.G...|:
x0C xE7 x5B xB6 x00 x00 x00 x00 x00 x00 x00 x00 x00 x00 x00 x00       ..[.............
x00 x00 x00 x00 x00 x00 x00 x00 x00 x00 x80 x3F x00 xA0 x8C x45       ...........?...E
x00 x50 x43 x46 x00 x00 x80 xBF x00 x00 x80 xBF x00 x00 x80 xBF       .PCF............
x00 x00 x80 xBF x00 x00 x80 xBF x00 x00 x80 x40 x00 x00 x80 x40       ...........@...@
x00 x00 x00 x00 x99 x99 x99 x3F xE1 x7A xB4 x3F x29 x5C xCF x3F       .......?.z.?)\.?
x1E x85 xEB x3F x33 x33 x03 x40 xD7 xA3 x10 x40 x52 xB8 x1E x40       ...?33.@...@R..@
xF6 x28 x2C x40 x99 x99 x39 x40 x14 xAE x47 x40 xB8 x1E x55 x40       .(,@..9@..G@..U@
x5C x8F x62 x40 xD7 xA3 x70 x40 x7B x14 x7E x40 x8F xC2 x85 x40       \.b@..p@{.~@...@
xCD xCC x8C x40 x00 x00 x48 x44 x8F xAA x97 x44 x1E x55 xCB x44       ...@..HD...D.U.D
x00 x00 xFF x44 x47 x55 x19 x45 x8F x2A x33 x45 x00 x00 x4D x45       ...DGU.E.*3E..ME
x47 xD5 x66 x45 x47 x55 x80 x45 x00 x40 x8D x45 xA4 x2A x9A x45       G.fEGU.E.@.E.*.E
x47 x15 xA7 x45 x00 x00 xB4 x45 xA4 xEA xC0 x45 x47 xD5 xCD x45       G..E...E...EG..E
x00 xC0 xDA x45 x00 x00 xAE x42 x00 x00 x8C x42 x00 x00 x00 x00       ...E...B...B....
x00 x00 x48 x42 x03 x00 x00 x00 x99 x99 x99 x3F xE1 x7A xB4 x3F       ..HB.......?.z.?
x29 x5C xCF x3F x1E x85 xEB x3F x33 x33 x03 x40 xD7 xA3 x10 x40       )\.?...?33.@...@
x52 xB8 x1E x40 xF6 x28 x2C x40 x99 x99 x39 x40 x14 xAE x47 x40       R..@.(,@..9@..G@
xB8 x1E x55 x40 x5C x8F x62 x40 xD7 xA3 x70 x40 x7B x14 x7E x40       ..U@\.b@..p@{.~@
x8F xC2 x85 x40 xCD xCC x8C x40 x00 x00 x48 x44 x8F xAA x97 x44       ...@...@..HD...D
x1E x55 xCB x44 x00 x00 xFF x44 x47 x55 x19 x45 x8F x2A x33 x45       .U.D...DGU.E.*3E
x00 x00 x4D x45 x47 xD5 x66 x45 x47 x55 x80 x45 x00 x40 x8D x45       ..MEG.fEGU.E.@.E
xA4 x2A x9A x45 x47 x15 xA7 x45 x00 x00 xB4 x45 xA4 xEA xC0 x45       .*.EG..E...E...E
x47 xD5 xCD x45 x00 xC0 xDA x45 x66 x66 xA6 x3F x58 x1B x00 x00       G..E...Eff.?X...
x00 x00 x00 x00 x01 x00 x00 x00 x00 x00 x2F x43 x00 x00 x00 x40       ........../C...@
x00 x00 x00 x00 xAB xAA xAA x40 x00 x00 x96 x42 x00 x00 x8C x42       .......@...B...B
x01 x00 x00 x00 x00 x00 x00 x00 x00 x00 x00 x00 x32 x00 x00 x00       ............2...
x04 x00 x00 x00 x00 x00 x00 x00 x01 x00 x00 x00 x00 x00 x00 x3F       ...............?
x01 x00 x00 x00 x00 x00 x00 x00 xA1 x52 x33 x01 x14 x00 x00 x00       .........R3.....
x04 x00 x00 x00 x03 x00 x00 x00 x01 x00 x00 x00 x14 x00 x00 x00       ................
x01 x00 x00 x00 x00 x00 x00 x00 x00 x00 x00 x00 x00 x00 x00 x00       ................
x00 x00 xC0 x3F x00 x00 x20 x40 x01 x00 x00 x00 x01 x00 x00 x00       ...?...@........
x00 x00 x00 x00 x00 x00 x80 x3F x0B x00 x00 x00 x07 x00 x00 x00       .......?........
x01 x00 x00 x00 x0E x00 x00 x00 x00 x00 x00 x00 x00 x00 x10 x41       ...............A
x00 x00 xA0 x40 x00 x00 x98 x41 x00 x00 x6C x42 x00 x00 x14 x42       ...@...A..lB...B
x00 x00 x80 x3F x00 x00 x00 x00 x00 x00 xFA x43 x00 x00 x00 x00       ...?.......C....
x04 x00 x00 x00 x00 x00 x00 x00 x00 x00 x00 x00 x00 x00 x00 x00       ................
x00 x00 x00 x00 x00 x00 x00 x00 x00 x00 x00 x00 x00 x00 x00 x00       ................
x00 x00 x00 x00 x00 x00 x00 x00 x00 x00 x00 x00 x00 x00 x00 x00       ................
x00 x00 x00 x00 x00 x00 x00 x00 x00 x00 x00 x00 x00 x00 x00 x00       ................
x00 x00 x00 x00 x00 x00 x00 x00 x00 x00 x00 x00 x00 x00 x00 x00       ................
x00 x00 x00 x00 x00 x00 x00 x00 x00 x00 x00 x00 x00 x00 x00 x00       ................
x00 x00 x00 x00 x00 x00 x00 x00 x00 x00 x00 x00 x00 x00 x00 x00       ................
x00 x00 x00 x00 x00 x00 x00 x00 x00 x00 x00 x00 x00 x00 x00 x00       ................
x00 x00 x00 x00 x00 x00 x00 x00 x00 x00 x00 x00 x00 x00 x00 x00       ................
x00 x00 x00 x00 x00 x00 x00 x00 x00 x00 x00 x00 x00 x00 x00 x00       ................
x00 x00 x00 x00 x00 x00 x00 x00 x00 x00 x00 x00 x00 x00 x00 x00       ................
x00 x00 x00 x00 x00 x00 x00 x00 x00 x00 x00 x00 x00 x00 x00 x00       ................
x00 x00 x00 x00 x00 x00 x00 x00 x00 x00 x00 x00 x00 x00 x00 x00       ................
x00 x00 x00 x00 x00 x00 x00 x00 x00 x00 x00 x00 x00 x00 x00 x00       ................
x00 x00 x00 x00 x00 x00 x00 x00 x00 x00 x00 x00 x00 x00 x00 x00       ................
x00 x00 x00 x00 x00 x00 x00 x00 x00 x00 x00 x00 x00 x00 x00 x00       ................
x00 x00 x00 x00                                                       ....

7/5/14 8:56:30 PM :Debug: commThreadExpectedReturnTime set to ms from now: 860
7/5/14 8:56:30 PM :Time: 0:01.894: SENT, 3 bytes
x50 x01 x00                                                           P..

7/5/14 8:56:30 PM :Debug: commThreadExpectedReturnTime set to ms from now: 20140
7/5/14 8:56:30 PM :Time: 0:02.005: SENT, 7 bytes
x52 x01 x00 x00 x00 x44 x01                                           R....D.

7/5/14 8:56:30 PM :Debug: Read page time: 210ms.
7/5/14 8:56:30 PM :Debug: Reading ECU Data, 0.5 complete
7/5/14 8:56:30 PM :Time: 0:02.154: Received, 324 bytes
x42 x00 x00 x00 x00 x00 x00 x00 x2D x00 x00 x00 x00 x00 x00 x00       B.......-.......
x19 x00 x00 x00 x18 x00 x00 x00 x43 x00 x00 x00 x45 x00 x00 x00       ........C...E...
x50 x00 x00 x00 x50 x00 x00 x00 x00 x00 x00 x00 x00 x00 x00 x00       P...P...........
x00 x00 x00 x00 x00 x00 x00 x00 x00 x00 x00 x00 x00 x00 x00 x00       ................
x00 x00 x00 x00 x27 x00 x00 x00 x44 x00 x00 x00 x40 x00 x00 x00       ....'...D...@...
x41 x00 x00 x00 x00 x00 x00 x00 x00 x00 x00 x00 x00 x00 x00 x00       A...............
x00 x00 x00 x00 x00 x00 x00 x00 x00 x00 x00 x00 x00 x00 x00 x00       ................
x00 x00 x00 x00 x00 x00 x00 x00 x29 x00 x00 x00 x00 x00 x00 x00       ........).......
x2F x00 x00 x00 x00 x00 x00 x00 x29 x00 x00 x00 x00 x00 x00 x00       /.......).......
x28 x00 x00 x00 x00 x00 x00 x00 x00 x00 x00 x00 x00 x00 x00 x00       (...............
x49 x00 x00 x00 x4B x00 x00 x00 x4D x00 x00 x00 x4F x00 x00 x00       I...K...M...O...
x1B x00 x00 x00 x1D x00 x00 x00 x31 x00 x00 x00 x32 x00 x00 x00       ........1...2...
x00 x00 x00 x00 x00 x00 x00 x00 x00 x00 x00 x00 x00 x00 x00 x00       ................
x00 x00 x00 x00 x00 x00 x00 x00 x00 x00 x00 x00 x01 x00 x00 x00       ................
x01 x00 x00 x00 x01 x00 x00 x00 x01 x00 x00 x00 x02 x00 x00 x00       ................
x00 x00 x00 x00 x01 x00 x00 x00 x01 x00 x00 x00 x00 x00 x00 x00       ................
x00 x00 x00 x00 x00 x00 x00 x00 x01 x00 x00 x00 x01 x00 x00 x00       ................
x01 x00 x00 x00 x00 x00 x00 x00 x00 x00 x00 x00 x26 x00 x00 x00       ............&...
x05 x00 x00 x00 x08 x00 x00 x00 x47 x00 x00 x00 x64 x00 x00 x00       ........G...d...
xC8 x00 x00 x00 x2C x01 x00 x00 x2C x01 x00 x00 xC8 x00 x00 x00       ....,...,.......
x00 x96 x00 x00                                                       ....

7/5/14 8:56:30 PM :Debug: commThreadExpectedReturnTime set to ms from now: 860
7/5/14 8:56:30 PM :Time: 0:02.197: SENT, 3 bytes
x50 x02 x00                                                           P..

7/5/14 8:56:30 PM :Debug: commThreadExpectedReturnTime set to ms from now: 20140
7/5/14 8:56:30 PM :Time: 0:02.307: SENT, 7 bytes
x52 x02 x00 x00 x00 x00 x04                                           R......

7/5/14 8:56:30 PM :Debug: Read page time: 210ms.
7/5/14 8:56:30 PM :Debug: Reading ECU Data, 0.75 complete
7/5/14 8:56:30 PM :Time: 0:02.456: Received, 1024 bytes
x42 x60 xC5 x3F xC2 x17 xC6 x3F x94 xA3 xC6 x3F xC3 xF5 xC8 x3F       B`.?...?...?...?
x66 x66 xC6 x3F x56 x9E x68 x3F x03 x78 x4B x3F x82 x73 x46 x3F       ff.?V.h?.xK?.sF?
x04 xAF x4A x3F xCD xCC x4C x3F x71 x75 x4C x3F x85 x44 x4E x3F       ..J?..L?quL?.DN?
x29 x5C x4F x3F x29 x5C x4F x3F x29 x5C x4F x3F x29 x5C x4F x3F       )\O?)\O?)\O?)\O?
xEF x1C xC4 x3F x92 x5C xC8 x3F x2A x8F xC6 x3F x44 xC1 xC6 x3F       ...?.\.?*..?D..?
xEB xE3 xC5 x3F xB4 x55 x4D x3F x29 x5C x4F x3F x98 xDB x49 x3F       ...?.UM?)\O?..I?
xF0 x13 x4F x3F x78 xB7 x3E x3F x82 x8D x33 x3F x93 x1E x36 x3F       ..O?x.>?..3?..6?
x7F xA2 x3E x3F x29 x5C x4F x3F x29 x5C x4F x3F x29 x5C x4F x3F       .>?)\O?)\O?)\O?
xAF x94 xC5 x3F x56 xD5 xC5 x3F x91 x29 xC7 x3F x71 xE2 xC5 x3F       ...?V..?.).?q..?
xA2 x29 xB5 x3F x1D x1C xEC x3D x00 x00 x00 x00 x00 x00 x00 x00       .).?...=........
x00 x00 x00 x00 x00 x00 x00 x00 x00 x00 x00 x00 x00 x00 x00 x00       ................
x00 x00 x00 x00 x00 x00 x00 x00 x00 x00 x00 x00 x00 x00 x00 x00       ................
x66 xF7 xC4 x3F x5A xF6 xDE x3F x81 x7A xC7 x3F x4E xB4 xCB x3F       f..?Z..?.z.?N..?
x6F x48 x9D x3F x00 x00 x00 x00 x00 x00 x00 x00 x00 x00 x00 x00       oH.?............
x00 x00 x00 x00 x00 x00 x00 x00 x00 x00 x00 x00 x00 x00 x00 x00       ................
x00 x00 x00 x00 x00 x00 x00 x00 x00 x00 x00 x00 x00 x00 x00 x00       ................
xEF xAA x14 x40 xC8 x27 x5C x40 xAE x62 x34 x40 x49 x81 x0F x40       ...@.'\@.b4@I..@
xBF x0D x08 x40 x56 xD6 x98 x3F xD6 x58 xFA x3E x00 x00 x00 x00       ...@V..?.X.>....
x00 x00 x00 x00 x00 x00 x00 x00 x00 x00 x00 x00 x00 x00 x00 x00       ................
x00 x00 x00 x00 x00 x00 x00 x00 x00 x00 x00 x00 x00 x00 x00 x00       ................
x19 x4B xF6 x40 xEC xA3 xBE x40 x69 x6E x96 x40 xD0 x44 x78 x40       .K.@...@in.@.Dx@
xD9 x5F x46 x40 x92 xCC x19 x40 xC9 x5A x1D x40 xCD x3E xE5 x3F       ._F@...@.Z.@.>.?
xB1 x31 x0C x40 x58 xC7 x04 x40 xB0 x37 xAF x3F xA3 xCE xA4 x3F       .1.@X..@.7.?...?
x00 x00 x00 x00 x00 x00 x00 x00 x00 x00 x00 x00 x00 x00 x00 x00       ................
xAF x47 x65 x41 x54 x5F x0B x41 x3C xDC xD1 x40 x88 xBA xAF x40       .GeAT_.A<..@...@
x83 xC2 xA3 x40 xAC xE1 x89 x40 x93 xDF x4B x40 xB2 xBA x55 x40       ...@...@..K@..U@
x59 x86 x38 x40 x19 xC9 x35 x40 x62 x2C x29 x40 x6D x53 x20 x40       Y.8@..5@b,)@mS.@
x26 xFC x12 x40 x00 x00 x00 x00 x00 x00 x00 x00 x00 x00 x00 x00       &..@............
x00 xD5 xAA x41 xDC xA7 x76 x41 x02 x41 x2F x41 xEA x78 x0C x41       ...A..vA.A/A.x.A
x36 xBA xBB x40 x06 x3C xA1 x40 xC7 x9F xA3 x40 x78 xA8 x8C x40       6..@.<.@...@x..@
xBE x30 x91 x40 xFB xCC x63 x40 x25 x08 x75 x40 x11 x6F x49 x40       .0.@..c@%.u@.oI@
x56 x2C x58 x40 x85 xEB x31 x40 x85 xEB x31 x40 x85 xEB x31 x40       V,X@..1@..1@..1@
xC8 x29 xA0 x41 x57 x7D x82 x41 x06 xAE x89 x41 x93 x9B x79 x41       .).AW}.A...A..yA
xF3 x33 x2F x41 x3A xC0 xF8 x40 xB8 xC8 xC7 x40 xD2 xD1 xEC x40       .3/A:..@...@...@
x62 x81 xD5 x40 x49 x49 xC4 x40 xC0 xF5 xB0 x40 x77 x9F x98 x40       b..@II.@...@w..@
x79 xE6 x90 x40 xEC x51 x80 x40 xEC x51 x80 x40 xEC x51 x80 x40       y..@.Q.@.Q.@.Q.@
xAC x1C x92 x41 x18 x6D x77 x41 x0D x86 x79 x41 x08 x55 x76 x41       ...A.mwA..yA.UvA
xED xCA x4F x41 x5C x6D x55 x41 xE4 x5C x0E x41 x5B xD6 x0E x41       ..OA\mUA.\.A[..A
xAD x86 x00 x41 xFA x9B xD8 x40 xC3 x58 xBA x40 x7E x38 xCD x40       ...A...@.X.@~8.@
x64 xDB xC2 x40 x29 x5C xB7 x40 x29 x5C xB7 x40 x29 x5C xB7 x40       d..@)\.@)\.@)\.@
x3D x51 x8B x41 xC7 xDC x75 x41 x80 xFF x72 x41 x17 x6A x75 x41       =Q.A..uA..rA.juA
xEE xE7 x74 x41 xB3 x30 x76 x41 x66 x88 x67 x41 x57 x11 x3F x41       ..tA.0vAf.gAW.?A
xD7 xC4 x2F x41 x6A x4D x1F x41 x47 x4E x10 x41 x9C x10 x07 x41       ../AjM.AGN.A...A
x83 x7C xF0 x40 xCD xCC xDC x40 xCD xCC xDC x40 xCD xCC xDC x40       .|.@...@...@...@
xEC x0A x88 x41 xF3 xF4 x75 x41 xB4 x02 x73 x41 xC9 x73 x74 x41       ...A..uA..sA.stA
xCA x36 x75 x41 x7F xFC x78 x41 xF5 x38 x7A x41 xA5 xA5 x76 x41       .6uA.xA.8zA..vA
x17 x16 x5A x41 x4C xB3 x2E x41 x0E x22 x38 x41 x67 x8F x2A x41       ..ZAL..A."8Ag.*A
x3D xD4 x18 x41 x14 xAE x13 x41 x14 xAE x13 x41 x14 xAE x13 x41       =..A...A...A...A
x95 xD4 x87 x41 xFA xC3 x75 x41 xB9 xBA x72 x41 xAE xD3 x74 x41       ...A..uA..rA..tA
xE8 x4D x75 x41 x4E xF3 x7A x41 xBA xF7 x7C x41 x40 x3D x7B x41       .MuAN.zA..|A@={A
xED x3F x7D x41 xE4 xD6 x71 x41 xF1 xA7 x6A x41 xA3 x8A x3E x41       .?}A..qA..jA..>A
x61 xBF x40 x41 x14 xAE x13 x41 x14 xAE x13 x41 x14 xAE x13 x41       a.@A...A...A...A
x07 xCE x87 x41 x46 x7D x75 x41 x35 xE4 x74 x41 x42 x98 x74 x41       ...AF}uA5.tAB.tA
xEE x9E x74 x41 xD4 xBE x77 x41 x96 xDC x7E x41 x61 x7C x7C x41       ..tA..wA..~Aa||A
x64 xB4 x7A x41 x18 x63 x7D x41 x97 xFC x80 x41 xF2 xDF x70 x41       d.zA.c}A...A..pA
xB7 x8F x6F x41 x8F xC2 x69 x41 x8F xC2 x69 x41 x8F xC2 x69 x41       ..oA..iA..iA..iA
xE8 xB1 x87 x41 xEE xE4 x75 x41 x96 x5D x73 x41 x77 xA6 x74 x41       ...A..uA.]sAw.tA
x25 x38 x74 x41 xBF xC5 x77 x41 xC2 x3C x7D x41 xC6 xD6 x7C x41       %8tA..wA.<}A..|A
x9E xD8 x7A x41 xE2 x3B x7D x41 x59 xF4 x7F x41 x41 x38 x80 x41       ..zA.;}AY.AA8.A
xDB xA7 x77 x41 x3D x0A x73 x41 x3D x0A x73 x41 x3D x0A x73 x41       ..wA=.sA=.sA=.sA
x7B x14 x88 x41 x00 x00 x74 x41 x48 xE1 x7A x41 x3D x0A x77 x41       {..A..tAH.zA=.wA
xEC x51 x74 x41 x1F x85 x77 x41 xCD xCC x7C x41 x14 xAE x7B x41       .QtA..wA..|A..{A
x9A x99 x79 x41 xD7 xA3 x7C x41 xC3 xF5 x80 x41 x48 xE1 x80 x41       ..yA..|A...AH..A
x7B x14 x7A x41 x66 x66 x72 x41 x66 x66 x72 x41 x66 x66 x72 x41       {.zAffrAffrAffrA

7/5/14 8:56:30 PM :Debug: commThreadExpectedReturnTime set to ms from now: 860
7/5/14 8:56:30 PM :Time: 0:02.487: SENT, 3 bytes
x50 x03 x00                                                           P..

7/5/14 8:56:30 PM :Debug: commThreadExpectedReturnTime set to ms from now: 20140
7/5/14 8:56:30 PM :Time: 0:02.597: SENT, 7 bytes
x52 x03 x00 x00 x00 x00 x04                                           R......

7/5/14 8:56:31 PM :Debug: Read page time: 210ms.
7/5/14 8:56:31 PM :Debug: Reading ECU Data, 1.0 complete
7/5/14 8:56:31 PM :Debug: Read All Data
7/5/14 8:56:31 PM :Time: 0:02.746: Received, 1024 bytes
xD5 x78 x29 x3F x29 x5C xF7 xC0 xA8 xC6 x85 xC1 xB8 x1E xB9 xC1       .x)?)\..........
x1B x2F xEB xC1 xDD x24 xFA xC1 x98 x6E x00 xC2 xEE x7C xF3 xC1       ./...$...n...|..
x02 x2B xF7 xC1 x7D x3F xD5 xC1 xCB xA1 xC5 xC1 x2F xDD xC8 xC1       .+..}?....../...
x56 x0E xC9 xC1 x14 xAE xCB xC1 x14 xAE xCB xC1 x14 xAE xCB xC1       V...............
xA8 xC6 x0B x3F x1B x2F xF5 xC0 x56 x0E x87 xC1 x23 xDB xBB xC1       ...?./..V...#...
xF6 x28 xEC xC1 x8D x97 xFA xC1 x98 x6E x00 xC2 x7D x3F xF5 xC1       .(.......n..}?..
x77 xBE xF3 xC1 x3D x0A xD7 xC1 xCF xF7 xC5 xC1 x9E xEF xC5 xC1       w...=...........
x89 x41 xE8 xC1 xFA x7E xCC xC1 xFA x7E xCC xC1 xFA x7E xCC xC1       .A...~...~...~..
x06 x81 x15 x3F x0A xD7 xFB xC0 x46 xB6 x85 xC1 x3F x35 xB8 xC1       ...?....F...?5..
x04 x56 xEC xC1 xF8 x53 xF9 xC1 x39 xB4 x00 xC2 xEC x51 xF4 xC1       .V...S..9....Q..
xDD x24 xF2 xC1 xF8 x53 xD3 xC1 x6F x12 xC1 xC1 x62 x10 xC8 xC1       .$...S..o...b...
x81 x95 xC5 xC1 x10 x58 xD1 xC1 x10 x58 xD1 xC1 x10 x58 xD1 xC1       .....X...X...X..
x06 x81 x15 x3F x56 x0E xF5 xC0 x46 xB6 x85 xC1 x31 x08 xBA xC1       ...?V...F...1...
xE5 xD0 xEA xC1 xF2 xD2 xF7 xC1 x68 x91 x00 xC2 xF4 xFD xF6 xC1       ........h.......
x02 x2B xF7 xC1 x62 x10 xD4 xC1 xC9 x76 xC4 xC1 xB8 x1E xC3 xC1       .+..b....v......
x93 x18 xCE xC1 xCF xF7 x0D xC2 xCF xF7 x0D xC2 xCF xF7 x0D xC2       ................
x06 x81 x15 x3F x81 x95 xFB xC0 xD3 x4D x84 xC1 x31 x08 xBA xC1       ...?.....M..1...
x23 xDB xE9 xC1 x35 x5E xFA xC1 x7B x14 x02 xC2 xD1 x22 xF1 xC1       #...5^..{...."..
xA0 x1A xF3 xC1 x64 x3B xCF xC1 xC3 xF5 xC2 xC1 xF0 xA7 xC0 xC1       ....d;..........
x04 x56 xC6 xC1 xE5 xD0 xC2 xC1 xE5 xD0 xC2 xC1 xE5 xD0 xC2 xC1       .V..............
x8D x97 xAE xBF x64 x3B xF7 xC0 xB0 x72 x86 xC1 x31 x08 xBA xC1       ....d;...r..1...
xB8 x1E xED xC1 x4A x0C xF8 xC1 x27 x31 x01 xC2 xC7 x4B xF7 xC1       ....J...'1...K..
x56 x0E xEF xC1 xD1 x22 xD3 xC1 xDF x4F xC5 xC1 x3B xDF xD9 xC1       V...."...O..;...
xF4 xFD xCA xC1 x10 x58 xCB xC1 x10 x58 xCB xC1 x10 x58 xCB xC1       .....X...X...X..
x8D x97 xAE x3F x0A xD7 x27 xC1 xE3 xA5 x85 xC1 x37 x89 xB3 xC1       ...?..'.....7...
xE5 xD0 xE0 xC1 x6D xE7 xF1 xC1 xBC x74 x01 xC2 x8F xC2 xF5 xC1       ....m....t......
x02 x2B xF7 xC1 x2F xDD xD4 xC1 xDF x4F xC5 xC1 xBC x74 xC3 xC1       .+../....O...t..
x00 x00 xC4 xC1 x7B x14 xCC xC1 x7B x14 xCC xC1 x7B x14 xCC xC1       ....{...{...{...
xF2 xD2 x1D x41 xF0 xA7 x26 xC1 x48 xE1 x3A xC1 x33 x33 x99 xC1       ...A..&.H.:.33..
x31 x08 xCE xC1 xEE x7C xDF xC1 x4C x37 x02 xC2 x7D x3F xF5 xC1       1....|..L7..}?..
x64 x3B xF1 xC1 xD5 x78 xD9 xC1 x19 x04 xCA xC1 xFA x7E xB6 xC1       d;...x.......~..
xB2 x9D xC3 xC1 x8F xC2 xC9 xC1 x8F xC2 xC9 xC1 x8F xC2 xC9 xC1       ................
x23 xDB x1D x41 xC9 x76 xAE x40 xF0 xA7 x36 x40 x2D xB2 x89 xC1       #..A.v.@..6@-...
x7F x6A x8C xC1 x06 x81 xA5 xC1 xAE x47 xCD xC1 xE1 x7A xDE xC1       j.......G...z..
x37 x89 xDD xC1 xC1 xCA xD9 xC1 x56 x0E xCF xC1 x48 xE1 xCA xC1       7.......V...H...
xCD xCC xD0 xC1 x9E xEF xDF xC1 x9E xEF xDF xC1 x9E xEF xDF xC1       ................
xF2 xD2 x1D x41 xC9 x76 xAE x40 xF0 xA7 x36 x40 xA0 x1A xAF xBE       ...A.v.@..6@....
x7F x6A x48 xC1 x77 xBE x81 xC1 x79 xE9 xAA xC1 x52 xB8 xDC xC1       jH.w...y...R...
x71 x3D xCE xC1 x29 x5C xC1 xC1 xDF x4F xC5 xC1 x08 xAC xCC xC1       q=..)\...O......
x85 xEB xD3 xC1 x77 xBE xFF xC1 x77 xBE xFF xC1 x77 xBE xFF xC1       ....w...w...w...
xF2 xD2 x1D x41 x12 x83 xB0 x40 xF0 xA7 x36 x40 x8B x6C x67 xBE       ...A...@..6@.lg.
x64 x3B x2F xC0 x58 x39 x74 xC0 xB4 xC8 x3E xC1 xC9 x76 x96 xC1       d;/.X9t...>..v..
xD3 x4D xA8 xC1 xD3 x4D xAC xC1 x14 xAE xA9 xC1 xF2 xD2 xB1 xC1       .M...M..........
x35 x5E xC8 xC1 x7D x3F xC9 xC1 x7D x3F xC9 xC1 x7D x3F xC9 xC1       5^..}?..}?..}?..
x23 xDB x1D x41 x75 x93 xB0 x40 xF0 xA7 x36 x40 x00 x00 x00 x00       #..Au..@..6@....
x73 x68 x41 xC0 x58 x39 x74 xC0 x2D xB2 xCD xC0 x4C x37 xF9 xC0       shA.X9t.-...L7..
x73 x68 x9B xC1 x48 xE1 xA6 xC1 x5E xBA x9F xC1 x71 x3D xA8 xC1       sh..H...^...q=..
x02 x2B xAB xC1 x5C x8F xAC xC1 x5C x8F xAC xC1 x5C x8F xAC xC1       .+..\...\...\...
xF2 xD2 x1D x41 x12 x83 xB0 x40 x73 x68 x31 x40 x8B x6C x67 xBE       ...A...@sh1@.lg.
x17 xD9 x2E xC0 x00 x00 x60 xC0 x37 x89 xD9 xC0 xCB xA1 x01 xC1       ......`.7.......
x5C x8F x0A xC1 x00 x00 x18 xC1 xA6 x9B x3C xC1 x56 x0E xA1 xC1       \.........<.V...
x75 x93 xA0 xC1 x7B x14 xA4 xC1 x7B x14 xA4 xC1 x7B x14 xA4 xC1       u...{...{...{...
xF2 xD2 x1D x41 x75 x93 xB0 x40 xF0 xA7 x36 x40 x00 x00 x00 x00       ...Au..@..6@....
xEC x51 x38 xC0 x58 x39 x74 xC0 xA4 x70 xCD xC0 xB8 x1E x05 xC1       .Q8.X9t..p......
xE5 xD0 x06 xC1 x12 x83 x08 xC1 x1F x85 x37 xC1 x6F x12 x37 xC1       ..........7.o.7.
x8F xC2 x59 xC1 x1D x5A x40 xC1 x1D x5A x40 xC1 x1D x5A x40 xC1       ..Y..Z@..Z@..Z@.
x00 x00 x1C x41 x75 x93 xB0 x40 xF0 xA7 x26 x40 x00 x00 x00 x00       ...Au..@..&@....
xEC x51 x38 xC0 x23 xDB x69 xC0 x9A x99 xC1 xC0 x7F x6A xDC xC0       .Q8.#.i.....j..
xB6 xF3 x05 xC1 xF2 xD2 x15 xC1 x58 x39 x3C xC1 x46 xB6 x3B xC1       ........X9<.F.;.
xF2 xD2 x3D xC1 x19 x04 x46 xC1 x19 x04 x46 xC1 x19 x04 x46 xC1       ..=...F...F...F.
x33 x33 xB3 x3E x48 xE1 xB2 x40 x12 x83 x00 x3F xC3 xF5 x68 x3F       33.>H..@...?..h?
x1B x2F x5D x3F x58 x39 x74 x3F xD5 x78 xA9 x3F xB6 xF3 xED xC0       ./]?X9t?.x.?....
x8F xC2 x95 x3F x79 xE9 x86 x3F x46 xB6 x03 x40 xA2 x45 x06 x40       ...?y..?F..@.E.@
x39 xB4 x28 x40 xCB xA1 x45 xC1 xCB xA1 x45 xC1 xCB xA1 x45 xC1       9.(@..E...E...E.

Time: 0:02.748: Processing Complete: 
7/5/14 8:56:31 PM :Debug: Real OchDelay for MyCar: 50, timeout=300
7/5/14 8:56:31 PM :Debug: commThreadExpectedReturnTime set to ms from now: 620
7/5/14 8:56:31 PM :Time: 0:02.800: SENT, 1 bytes
x4F                                                                   O

7/5/14 8:56:31 PM :Time: 0:02.849: Received, 52 bytes
xB0 x04 x00 x00 xE8 xFD x18 x42 xD0 xA9 x7C x42 x00 x00 x00 x00       .......B..|B....
x57 x6A x25 x3F x03 x30 x10 x41 x00 x00 x00 x00 x01 x08 x80 x3C       Wj%?.0.A.......<
x5F x00 x00 x00 x8A x9D x38 x42 x00 x00 xC0 x7F x01 x00 x00 x00       _.....8B.......
xE2 xE8 x31 x42                                                       ..1B

7/5/14 8:56:31 PM :Debug: old style time to read outpc: 49 ms.
7/5/14 8:56:31 PM :Info: dr: 0:47
7/5/14 8:56:31 PM :Debug: Range Sort Time: 0
7/5/14 8:56:31 PM :Debug: Real OchDelay for MyCar: 50, timeout=300
7/5/14 8:56:31 PM :Debug: commThreadExpectedReturnTime set to ms from now: 620
7/5/14 8:56:31 PM :Time: 0:02.859: SENT, 1 bytes
x4F                                                                   O

7/5/14 8:56:31 PM :Debug: old style time to read outpc: 49 ms.
7/5/14 8:56:31 PM :Time: 0:02.908: Received, 52 bytes
xB0 x04 x00 x00 xE8 xFD x18 x42 xD0 xA9 x7C x42 x00 x00 x00 x00       .......B..|B....
x57 x6A x25 x3F x03 x30 x10 x41 x00 x00 x00 x00 x01 x08 x80 x3C       Wj%?.0.A.......<
x5F x00 x00 x00 x8A x9D x38 x42 x00 x00 xC0 x7F x01 x00 x00 x00       _.....8B.......
xE2 xE8 x31 x42                                                       ..1B

7/5/14 8:56:31 PM :Debug: Real OchDelay for MyCar: 50, timeout=300
7/5/14 8:56:31 PM :Debug: commThreadExpectedReturnTime set to ms from now: 620
7/5/14 8:56:31 PM :Time: 0:02.918: SENT, 1 bytes
x4F                                                                   O

7/5/14 8:56:31 PM :Debug: old style time to read outpc: 49 ms.
7/5/14 8:56:31 PM :Time: 0:02.967: Received, 52 bytes
xB0 x04 x00 x00 xE8 xFD x18 x42 xD0 xA9 x7C x42 x00 x00 x00 x00       .......B..|B....
x57 x6A x25 x3F x03 x30 x10 x41 x00 x00 x00 x00 x01 x08 x80 x3C       Wj%?.0.A.......<
x5F x00 x00 x00 x8A x9D x38 x42 x00 x00 xC0 x7F x01 x00 x00 x00       _.....8B.......
xE2 xE8 x31 x42                                                       ..1B

7/5/14 8:56:31 PM :Debug: Real OchDelay for MyCar: 50, timeout=300
7/5/14 8:56:31 PM :Debug: commThreadExpectedReturnTime set to ms from now: 620
7/5/14 8:56:31 PM :Time: 0:02.981: SENT, 1 bytes
x4F                                                                   O

7/5/14 8:56:31 PM :Time: 0:03.031: Received, 52 bytes
xAF x04 x00 x00 xE8 x51 x14 x42 xE4 x5F x80 x42 x00 x00 x00 x00       .....Q.B._.B....
x5D xCA x25 x3F x03 x30 x10 x41 x00 x00 x00 x00 x01 x08 x80 x3C       ].%?.0.A.......<
x5F x00 x00 x00 x8A x9D x38 x42 x00 x00 xC0 x7F x01 x00 x00 x00       _.....8B.......
x60 x6D x2F x42                                                       `m/B

7/5/14 8:56:31 PM :Debug: old style time to read outpc: 50 ms.
7/5/14 8:56:31 PM :Debug: Real OchDelay for MyCar: 50, timeout=300
7/5/14 8:56:31 PM :Debug: commThreadExpectedReturnTime set to ms from now: 620
7/5/14 8:56:31 PM :Time: 0:03.045: SENT, 1 bytes
x4F                                                                   O

7/5/14 8:56:31 PM :Debug: old style time to read outpc: 49 ms.
7/5/14 8:56:31 PM :Time: 0:03.094: Received, 52 bytes
xAF x04 x00 x00 xE8 x51 x14 x42 xE4 x5F x80 x42 x00 x00 x00 x00       .....Q.B._.B....
x5D xCA x25 x3F x03 x30 x10 x41 x00 x00 x00 x00 x01 x08 x80 x3C       ].%?.0.A.......<
x5F x00 x00 x00 x8A x9D x38 x42 x00 x00 xC0 x7F x01 x00 x00 x00       _.....8B.......
x60 x6D x2F x42                                                       `m/B

7/5/14 8:56:31 PM :Debug: Real OchDelay for MyCar: 50, timeout=300
7/5/14 8:56:31 PM :Debug: commThreadExpectedReturnTime set to ms from now: 620
7/5/14 8:56:31 PM :Time: 0:03.109: SENT, 1 bytes
x4F                                                                   O

7/5/14 8:56:31 PM :Debug: old style time to read outpc: 50 ms.
7/5/14 8:56:31 PM :Time: 0:03.159: Received, 52 bytes
xAF x04 x00 x00 xE8 x51 x14 x42 xE4 x5F x80 x42 x00 x00 x00 x00       .....Q.B._.B....
x5D xCA x25 x3F x03 x30 x10 x41 x00 x00 x00 x00 x01 x08 x80 x3C       ].%?.0.A.......<
x5F x00 x00 x00 x8A x9D x38 x42 x00 x00 xC0 x7F x01 x00 x00 x00       _.....8B.......
x60 x6D x2F x42                                                       `m/B

7/5/14 8:56:31 PM :Debug: Real OchDelay for MyCar: 50, timeout=300
7/5/14 8:56:31 PM :Debug: commThreadExpectedReturnTime set to ms from now: 620
7/5/14 8:56:31 PM :Time: 0:03.175: SENT, 1 bytes
x4F                                                                   O

7/5/14 8:56:31 PM :Debug: old style time to read outpc: 49 ms.
7/5/14 8:56:31 PM :Time: 0:03.224: Received, 52 bytes
xAF x04 x00 x00 xE8 x51 x14 x42 xE4 x5F x80 x42 x00 x00 x00 x00       .....Q.B._.B....
x5D xCA x25 x3F x03 x30 x10 x41 x00 x00 x00 x00 x01 x08 x80 x3C       ].%?.0.A.......<
x5F x00 x00 x00 x8A x9D x38 x42 x00 x00 xC0 x7F x01 x00 x00 x00       _.....8B.......
x60 x6D x2F x42                                                       `m/B

7/5/14 8:56:31 PM :Debug: Real OchDelay for MyCar: 50, timeout=300
7/5/14 8:56:31 PM :Debug: commThreadExpectedReturnTime set to ms from now: 620
7/5/14 8:56:31 PM :Time: 0:03.241: SENT, 1 bytes
x4F                                                                   O

7/5/14 8:56:31 PM :Debug: old style time to read outpc: 49 ms.
7/5/14 8:56:31 PM :Time: 0:03.290: Received, 52 bytes
xB0 x04 x00 x00 x00 x99 x18 x42 xB0 xBE x7B x42 x00 x00 x00 x00       .......B..{B....
x3F xEA x23 x3F x05 x54 x10 x41 x00 x00 x00 x00 x02 x0E xE0 x3C       ?.#?.T.A.......<
x4B x00 x00 x00 x93 x33 x39 x42 x00 x00 xC0 x7F x01 x00 x00 x00       K....39B.......
x6C x62 x31 x42                                                       lb1B

7/5/14 8:56:31 PM :Debug: Real OchDelay for MyCar: 50, timeout=300
7/5/14 8:56:31 PM :Debug: commThreadExpectedReturnTime set to ms from now: 620
7/5/14 8:56:31 PM :Time: 0:03.307: SENT, 1 bytes
x4F                                                                   O

7/5/14 8:56:31 PM :Debug: old style time to read outpc: 49 ms.
7/5/14 8:56:31 PM :Debug: Real OchDelay for MyCar: 50, timeout=300
7/5/14 8:56:31 PM :Debug: commThreadExpectedReturnTime set to ms from now: 620
7/5/14 8:56:31 PM :Time: 0:03.356: Received, 52 bytes
xB0 x04 x00 x00 x00 x99 x18 x42 xB0 xBE x7B x42 x00 x00 x00 x00       .......B..{B....
x3F xEA x23 x3F x05 x54 x10 x41 x00 x00 x00 x00 x02 x0E xE0 x3C       ?.#?.T.A.......<
x4B x00 x00 x00 x93 x33 x39 x42 x00 x00 xC0 x7F x01 x00 x00 x00       K....39B.......
x6C x62 x31 x42                                                       lb1B

7/5/14 8:56:31 PM :Time: 0:03.373: SENT, 1 bytes
x4F                                                                   O

7/5/14 8:56:31 PM :Debug: old style time to read outpc: 50 ms.
7/5/14 8:56:31 PM :Time: 0:03.423: Received, 52 bytes
xB0 x04 x00 x00 x00 x99 x18 x42 xB0 xBE x7B x42 x00 x00 x00 x00       .......B..{B....
x3F xEA x23 x3F x05 x54 x10 x41 x00 x00 x00 x00 x02 x0E xE0 x3C       ?.#?.T.A.......<
x4B x00 x00 x00 x93 x33 x39 x42 x00 x00 xC0 x7F x01 x00 x00 x00       K....39B.......
x6C x62 x31 x42                                                       lb1B

7/5/14 8:56:31 PM :Debug: Real OchDelay for MyCar: 50, timeout=300
7/5/14 8:56:31 PM :Debug: commThreadExpectedReturnTime set to ms from now: 620
7/5/14 8:56:31 PM :Time: 0:03.445: SENT, 1 bytes
x4F                                                                   O

7/5/14 8:56:31 PM :Debug: old style time to read outpc: 51 ms.
7/5/14 8:56:31 PM :Time: 0:03.495: Received, 52 bytes
xB0 x04 x00 x00 x00 x99 x18 x42 xB0 xBE x7B x42 x00 x00 x00 x00       .......B..{B....
x3F xEA x23 x3F x05 x54 x10 x41 x00 x00 x00 x00 x02 x0E xE0 x3C       ?.#?.T.A.......<
x4B x00 x00 x00 x93 x33 x39 x42 x00 x00 xC0 x7F x01 x00 x00 x00       K....39B.......
x6C x62 x31 x42                                                       lb1B

7/5/14 8:56:31 PM :Debug: Real OchDelay for MyCar: 50, timeout=300
7/5/14 8:56:31 PM :Debug: commThreadExpectedReturnTime set to ms from now: 620
7/5/14 8:56:31 PM :Time: 0:03.523: SENT, 1 bytes
x4F                                                                   O

7/5/14 8:56:31 PM :Time: 0:03.572: Received, 52 bytes
xB0 x04 x00 x00 x00 x99 x18 x42 xB0 xBE x7B x42 x00 x00 x00 x00       .......B..{B....
x3F xEA x23 x3F x05 x54 x10 x41 x00 x00 x00 x00 x02 x0E xE0 x3C       ?.#?.T.A.......<
x4B x00 x00 x00 x93 x33 x39 x42 x00 x00 xC0 x7F x01 x00 x00 x00       K....39B.......
x6C x62 x31 x42                                                       lb1B

7/5/14 8:56:31 PM :Debug: old style time to read outpc: 50 ms.
7/5/14 8:56:31 PM :Debug: Real OchDelay for MyCar: 50, timeout=300
7/5/14 8:56:31 PM :Debug: commThreadExpectedReturnTime set to ms from now: 620
7/5/14 8:56:31 PM :Time: 0:03.587: SENT, 1 bytes
x4F                                                                   O

7/5/14 8:56:32 PM :Debug: old style time to read outpc: 49 ms.
7/5/14 8:56:32 PM :Time: 0:03.636: Received, 52 bytes
xAF x04 x00 x00 x50 xC8 x19 x42 xA8 xF4 x7D x42 x00 x00 x00 x00       ....P..B..}B....
x63 x2A x26 x3F x05 x48 x10 x41 x00 x00 x00 x00 x02 x0C xC0 x3C       c*&?.H.A.......<
x4D x00 x00 x00 x93 x33 x39 x42 x00 x00 xC0 x7F x01 x00 x00 x00       M....39B.......
x66 xD3 x32 x42                                                       f.2B

7/5/14 8:56:32 PM :Debug: Real OchDelay for MyCar: 50, timeout=300
7/5/14 8:56:32 PM :Debug: commThreadExpectedReturnTime set to ms from now: 620
7/5/14 8:56:32 PM :Time: 0:03.652: SENT, 1 bytes
x4F                                                                   O

7/5/14 8:56:32 PM :Debug: old style time to read outpc: 49 ms.
7/5/14 8:56:32 PM :Time: 0:03.701: Received, 52 bytes
xAF x04 x00 x00 x50 xC8 x19 x42 xA8 xF4 x7D x42 x00 x00 x00 x00       ....P..B..}B....
x63 x2A x26 x3F x05 x48 x10 x41 x00 x00 x00 x00 x02 x0C xC0 x3C       c*&?.H.A.......<
x4D x00 x00 x00 x93 x33 x39 x42 x00 x00 xC0 x7F x01 x00 x00 x00       M....39B.......
x66 xD3 x32 x42                                                       f.2B

7/5/14 8:56:32 PM :Debug: Real OchDelay for MyCar: 50, timeout=300
7/5/14 8:56:32 PM :Debug: commThreadExpectedReturnTime set to ms from now: 620
7/5/14 8:56:32 PM :Time: 0:03.718: SENT, 1 bytes
x4F                                                                   O

7/5/14 8:56:32 PM :Debug: old style time to read outpc: 50 ms.
7/5/14 8:56:32 PM :Time: 0:03.768: Received, 52 bytes
xAF x04 x00 x00 x50 xC8 x19 x42 xA8 xF4 x7D x42 x00 x00 x00 x00       ....P..B..}B....
x63 x2A x26 x3F x05 x48 x10 x41 x00 x00 x00 x00 x02 x0C xC0 x3C       c*&?.H.A.......<
x4D x00 x00 x00 x93 x33 x39 x42 x00 x00 xC0 x7F x01 x00 x00 x00       M....39B.......
x66 xD3 x32 x42                                                       f.2B

7/5/14 8:56:32 PM :Debug: Real OchDelay for MyCar: 50, timeout=300
7/5/14 8:56:32 PM :Debug: commThreadExpectedReturnTime set to ms from now: 620
7/5/14 8:56:32 PM :Time: 0:03.785: SENT, 1 bytes
x4F                                                                   O

7/5/14 8:56:32 PM :Debug: old style time to read outpc: 49 ms.
7/5/14 8:56:32 PM :Time: 0:03.834: Received, 52 bytes
xAF x04 x00 x00 x50 xC8 x19 x42 xA8 xF4 x7D x42 x00 x00 x00 x00       ....P..B..}B....
x63 x2A x26 x3F x05 x48 x10 x41 x00 x00 x00 x00 x02 x0C xC0 x3C       c*&?.H.A.......<
x4D x00 x00 x00 x93 x33 x39 x42 x00 x00 xC0 x7F x01 x00 x00 x00       M....39B.......
x66 xD3 x32 x42                                                       f.2B

7/5/14 8:56:32 PM :Debug: Real OchDelay for MyCar: 50, timeout=300
7/5/14 8:56:32 PM :Debug: commThreadExpectedReturnTime set to ms from now: 620
7/5/14 8:56:32 PM :Time: 0:03.856: SENT, 1 bytes
x4F                                                                   O

7/5/14 8:56:32 PM :Debug: old style time to read outpc: 50 ms.
7/5/14 8:56:32 PM :Time: 0:03.906: Received, 52 bytes
xB0 x04 x00 x00 x18 x02 x18 x42 xD0 xA9 x7C x42 x00 x00 x00 x00       .......B..|B....
x51 x0A x25 x3F x05 x54 x10 x41 x00 x00 x00 x00 x02 x0E xE0 x3C       Q.%?.T.A.......<
x5D x00 x00 x00 x8A x9D x38 x42 x00 x00 xC0 x7F x01 x00 x00 x00       ].....8B.......
x06 x2C x31 x42                                                       .,1B

7/5/14 8:56:32 PM :Debug: Real OchDelay for MyCar: 50, timeout=300
7/5/14 8:56:32 PM :Debug: commThreadExpectedReturnTime set to ms from now: 620
7/5/14 8:56:32 PM :Time: 0:03.923: SENT, 1 bytes
x4F                                                                   O

7/5/14 8:56:32 PM :Debug: old style time to read outpc: 49 ms.
7/5/14 8:56:32 PM :Time: 0:03.972: Received, 52 bytes
xB0 x04 x00 x00 x18 x02 x18 x42 xD0 xA9 x7C x42 x00 x00 x00 x00       .......B..|B....
x51 x0A x25 x3F x05 x54 x10 x41 x00 x00 x00 x00 x02 x0E xE0 x3C       Q.%?.T.A.......<
x5D x00 x00 x00 x8A x9D x38 x42 x00 x00 xC0 x7F x01 x00 x00 x00       ].....8B.......
x06 x2C x31 x42                                                       .,1B

7/5/14 8:56:32 PM :Debug: Real OchDelay for MyCar: 50, timeout=300
7/5/14 8:56:32 PM :Debug: commThreadExpectedReturnTime set to ms from now: 620
7/5/14 8:56:32 PM :Time: 0:03.994: SENT, 1 bytes
x4F                                                                   O

7/5/14 8:56:32 PM :Debug: old style time to read outpc: 50 ms.
7/5/14 8:56:32 PM :Time: 0:04.043: Received, 52 bytes
xB0 x04 x00 x00 x18 x02 x18 x42 xD0 xA9 x7C x42 x00 x00 x00 x00       .......B..|B....
x51 x0A x25 x3F x05 x54 x10 x41 x00 x00 x00 x00 x02 x0E xE0 x3C       Q.%?.T.A.......<
x5D x00 x00 x00 x8A x9D x38 x42 x00 x00 xC0 x7F x01 x00 x00 x00       ].....8B.......
x06 x2C x31 x42                                                       .,1B

7/5/14 8:56:32 PM :Debug: Real OchDelay for MyCar: 50, timeout=300
7/5/14 8:56:32 PM :Debug: commThreadExpectedReturnTime set to ms from now: 620
7/5/14 8:56:32 PM :Time: 0:04.060: SENT, 1 bytes
x4F                                                                   O

7/5/14 8:56:32 PM :Debug: old style time to read outpc: 49 ms.
7/5/14 8:56:32 PM :Time: 0:04.109: Received, 52 bytes
xB0 x04 x00 x00 x18 x02 x18 x42 xD0 xA9 x7C x42 x00 x00 x00 x00       .......B..|B....
x51 x0A x25 x3F x05 x54 x10 x41 x00 x00 x00 x00 x02 x0E xE0 x3C       Q.%?.T.A.......<
x5D x00 x00 x00 x8A x9D x38 x42 x00 x00 xC0 x7F x01 x00 x00 x00       ].....8B.......
x06 x2C x31 x42                                                       .,1B

7/5/14 8:56:32 PM :Debug: Real OchDelay for MyCar: 50, timeout=300
7/5/14 8:56:32 PM :Debug: commThreadExpectedReturnTime set to ms from now: 620
7/5/14 8:56:32 PM :Time: 0:04.126: SENT, 1 bytes
x4F                                                                   O

7/5/14 8:56:32 PM :Debug: old style time to read outpc: 49 ms.
7/5/14 8:56:32 PM :Time: 0:04.175: Received, 52 bytes
xB0 x04 x00 x00 x18 x02 x18 x42 xD0 xA9 x7C x42 x00 x00 x00 x00       .......B..|B....
x51 x0A x25 x3F x05 x54 x10 x41 x00 x00 x00 x00 x02 x0E xE0 x3C       Q.%?.T.A.......<
x5D x00 x00 x00 x8A x9D x38 x42 x00 x00 xC0 x7F x01 x00 x00 x00       ].....8B.......
x06 x2C x31 x42                                                       .,1B

7/5/14 8:56:32 PM :Debug: Real OchDelay for MyCar: 50, timeout=300
7/5/14 8:56:32 PM :Debug: commThreadExpectedReturnTime set to ms from now: 620
7/5/14 8:56:32 PM :Time: 0:04.192: SENT, 1 bytes
x4F                                                                   O

7/5/14 8:56:32 PM :Debug: old style time to read outpc: 49 ms.
7/5/14 8:56:32 PM :Time: 0:04.241: Received, 52 bytes
xB0 x04 x00 x00 x18 x76 x11 x42 x70 xD0 x7F x42 x00 x00 x00 x00       .....v.Bp.B....
x45 x4A x24 x3F x04 x3C x10 x41 x00 x00 x00 x00 x01 x0A xA0 x3C       EJ$?.<.A.......<
x59 x00 x00 x00 x52 x19 x35 x42 x00 x00 xC0 x7F x01 x00 x00 x00       Y...R.5B.......
xAE x0C x2D x42                                                       ..-B

7/5/14 8:56:32 PM :Debug: Real OchDelay for MyCar: 50, timeout=300
7/5/14 8:56:32 PM :Debug: commThreadExpectedReturnTime set to ms from now: 620
7/5/14 8:56:32 PM :Time: 0:04.264: SENT, 1 bytes
x4F                                                                   O

7/5/14 8:56:32 PM :Debug: old style time to read outpc: 56 ms.
7/5/14 8:56:32 PM :Time: 0:04.314: Received, 52 bytes
xB0 x04 x00 x00 x18 x76 x11 x42 x70 xD0 x7F x42 x00 x00 x00 x00       .....v.Bp.B....
x45 x4A x24 x3F x04 x3C x10 x41 x00 x00 x00 x00 x01 x0A xA0 x3C       EJ$?.<.A.......<
x59 x00 x00 x00 x52 x19 x35 x42 x00 x00 xC0 x7F x01 x00 x00 x00       Y...R.5B.......
xAE x0C x2D x42                                                       ..-B

7/5/14 8:56:32 PM :Debug: Real OchDelay for MyCar: 50, timeout=300
7/5/14 8:56:32 PM :Debug: commThreadExpectedReturnTime set to ms from now: 620
7/5/14 8:56:32 PM :Time: 0:04.329: SENT, 1 bytes
x4F                                                                   O

7/5/14 8:56:32 PM :Debug: old style time to read outpc: 49 ms.
7/5/14 8:56:32 PM :Time: 0:04.378: Received, 52 bytes
xB0 x04 x00 x00 x18 x76 x11 x42 x70 xD0 x7F x42 x00 x00 x00 x00       .....v.Bp.B....
x45 x4A x24 x3F x04 x3C x10 x41 x00 x00 x00 x00 x01 x0A xA0 x3C       EJ$?.<.A.......<
x59 x00 x00 x00 x52 x19 x35 x42 x00 x00 xC0 x7F x01 x00 x00 x00       Y...R.5B.......
xAE x0C x2D x42                                                       ..-B

7/5/14 8:56:32 PM :Debug: Real OchDelay for MyCar: 50, timeout=300
7/5/14 8:56:32 PM :Debug: commThreadExpectedReturnTime set to ms from now: 620
7/5/14 8:56:32 PM :Time: 0:04.394: SENT, 1 bytes
x4F                                                                   O

7/5/14 8:56:32 PM :Debug: old style time to read outpc: 50 ms.
7/5/14 8:56:32 PM :Time: 0:04.444: Received, 52 bytes
xB0 x04 x00 x00 x18 x76 x11 x42 x70 xD0 x7F x42 x00 x00 x00 x00       .....v.Bp.B....
x45 x4A x24 x3F x04 x3C x10 x41 x00 x00 x00 x00 x01 x0A xA0 x3C       EJ$?.<.A.......<
x59 x00 x00 x00 x52 x19 x35 x42 x00 x00 xC0 x7F x01 x00 x00 x00       Y...R.5B.......
xAE x0C x2D x42                                                       ..-B

7/5/14 8:56:32 PM :Debug: Real OchDelay for MyCar: 50, timeout=300
7/5/14 8:56:32 PM :Debug: commThreadExpectedReturnTime set to ms from now: 620
7/5/14 8:56:32 PM :Time: 0:04.466: SENT, 1 bytes
x4F                                                                   O

7/5/14 8:56:32 PM :Time: 0:04.516: Received, 52 bytes
xB0 x04 x00 x00 xD8 x2C x1B x42 xA8 x66 x7D x42 x00 x00 x00 x00       .....,.B.f}B....
x1B xAA x21 x3F x08 x78 x10 x41 x00 x00 x00 x00 x01 x0A x20 x3D       ...?.x.A.......=
x56 x00 x00 x00 x8A x9D x38 x42 x00 x00 xC0 x7F x01 x00 x00 x00       V.....8B.......
x4C xBB x33 x42                                                       L.3B

7/5/14 8:56:32 PM :Debug: old style time to read outpc: 50 ms.
7/5/14 8:56:32 PM :Debug: Real OchDelay for MyCar: 50, timeout=300
7/5/14 8:56:32 PM :Debug: commThreadExpectedReturnTime set to ms from now: 620
7/5/14 8:56:32 PM :Time: 0:04.531: SENT, 1 bytes
x4F                                                                   O

7/5/14 8:56:32 PM :Debug: old style time to read outpc: 49 ms.
7/5/14 8:56:32 PM :Time: 0:04.580: Received, 52 bytes
xB0 x04 x00 x00 xD8 x2C x1B x42 xA8 x66 x7D x42 x00 x00 x00 x00       .....,.B.f}B....
x1B xAA x21 x3F x08 x78 x10 x41 x00 x00 x00 x00 x01 x0A x20 x3D       ...?.x.A.......=
x56 x00 x00 x00 x8A x9D x38 x42 x00 x00 xC0 x7F x01 x00 x00 x00       V.....8B.......
x4C xBB x33 x42                                                       L.3B

7/5/14 8:56:32 PM :Debug: Real OchDelay for MyCar: 50, timeout=300
7/5/14 8:56:32 PM :Debug: commThreadExpectedReturnTime set to ms from now: 620
7/5/14 8:56:32 PM :Time: 0:04.597: SENT, 1 bytes
x4F                                                                   O

7/5/14 8:56:33 PM :Debug: old style time to read outpc: 49 ms.
7/5/14 8:56:33 PM :Time: 0:04.647: Received, 52 bytes
xB0 x04 x00 x00 xD8 x2C x1B x42 xA8 x66 x7D x42 x00 x00 x00 x00       .....,.B.f}B....
x1B xAA x21 x3F x08 x78 x10 x41 x00 x00 x00 x00 x01 x0A x20 x3D       ...?.x.A.......=
x56 x00 x00 x00 x8A x9D x38 x42 x00 x00 xC0 x7F x01 x00 x00 x00       V.....8B.......
x4C xBB x33 x42                                                       L.3B

7/5/14 8:56:33 PM :Debug: Real OchDelay for MyCar: 50, timeout=300
7/5/14 8:56:33 PM :Debug: commThreadExpectedReturnTime set to ms from now: 620
7/5/14 8:56:33 PM :Time: 0:04.663: SENT, 1 bytes
x4F                                                                   O

7/5/14 8:56:33 PM :Time: 0:04.713: Received, 52 bytes
xB0 x04 x00 x00 xD8 x2C x1B x42 xA8 x66 x7D x42 x00 x00 x00 x00       .....,.B.f}B....
x1B xAA x21 x3F x08 x78 x10 x41 x00 x00 x00 x00 x01 x0A x20 x3D       ...?.x.A.......=
x56 x00 x00 x00 x8A x9D x38 x42 x00 x00 xC0 x7F x01 x00 x00 x00       V.....8B.......
x4C xBB x33 x42                                                       L.3B

7/5/14 8:56:33 PM :Debug: old style time to read outpc: 49 ms.
7/5/14 8:56:33 PM :Debug: Real OchDelay for MyCar: 50, timeout=300
7/5/14 8:56:33 PM :Debug: commThreadExpectedReturnTime set to ms from now: 620
7/5/14 8:56:33 PM :Time: 0:04.729: SENT, 1 bytes
x4F                                                                   O

7/5/14 8:56:33 PM :Debug: old style time to read outpc: 50 ms.
7/5/14 8:56:33 PM :Time: 0:04.780: Received, 52 bytes
xB0 x04 x00 x00 xD8 x2C x1B x42 xA8 x66 x7D x42 x00 x00 x00 x00       .....,.B.f}B....
x1B xAA x21 x3F x08 x78 x10 x41 x00 x00 x00 x00 x01 x0A x20 x3D       ...?.x.A.......=
x56 x00 x00 x00 x8A x9D x38 x42 x00 x00 xC0 x7F x01 x00 x00 x00       V.....8B.......
x4C xBB x33 x42                                                       L.3B

7/5/14 8:56:33 PM :Debug: Real OchDelay for MyCar: 50, timeout=300
7/5/14 8:56:33 PM :Debug: commThreadExpectedReturnTime set to ms from now: 620
7/5/14 8:56:33 PM :Time: 0:04.797: SENT, 1 bytes
x4F                                                                   O

7/5/14 8:56:33 PM :Debug: old style time to read outpc: 50 ms.
7/5/14 8:56:33 PM :Time: 0:04.848: Received, 52 bytes
xB0 x04 x00 x00 x30 x76 x0E x42 x08 x71 x7F x42 x00 x00 x00 x00       ....0v.B.qB....
x1B xAA x21 x3F x08 x78 x10 x41 x00 x00 x00 x00 x01 x0A x20 x3D       ...?.x.A.......=
x5E x00 x00 x00 x77 x71 x37 x42 x00 x00 xC0 x7F x01 x00 x00 x00       ^...wq7B.......
xE6 xB4 x2A x42                                                       ..*B

7/5/14 8:56:33 PM :Debug: Real OchDelay for MyCar: 50, timeout=300
7/5/14 8:56:33 PM :Debug: commThreadExpectedReturnTime set to ms from now: 620
7/5/14 8:56:33 PM :Time: 0:04.866: SENT, 1 bytes
x4F                                                                   O

7/5/14 8:56:33 PM :Debug: old style time to read outpc: 50 ms.
7/5/14 8:56:33 PM :Time: 0:04.916: Received, 52 bytes
xB0 x04 x00 x00 x30 x76 x0E x42 x08 x71 x7F x42 x00 x00 x00 x00       ....0v.B.qB....
x1B xAA x21 x3F x08 x78 x10 x41 x00 x00 x00 x00 x01 x0A x20 x3D       ...?.x.A.......=
x5E x00 x00 x00 x77 x71 x37 x42 x00 x00 xC0 x7F x01 x00 x00 x00       ^...wq7B.......
xE6 xB4 x2A x42                                                       ..*B

7/5/14 8:56:33 PM :Debug: Real OchDelay for MyCar: 50, timeout=300
7/5/14 8:56:33 PM :Debug: commThreadExpectedReturnTime set to ms from now: 620
7/5/14 8:56:33 PM :Time: 0:04.932: SENT, 1 bytes
x4F                                                                   O

7/5/14 8:56:33 PM :Debug: old style time to read outpc: 49 ms.
7/5/14 8:56:33 PM :Time: 0:04.981: Received, 52 bytes
xB0 x04 x00 x00 x30 x76 x0E x42 x08 x71 x7F x42 x00 x00 x00 x00       ....0v.B.qB....
x1B xAA x21 x3F x08 x78 x10 x41 x00 x00 x00 x00 x01 x0A x20 x3D       ...?.x.A.......=
x5E x00 x00 x00 x77 x71 x37 x42 x00 x00 xC0 x7F x01 x00 x00 x00       ^...wq7B.......
xE6 xB4 x2A x42                                                       ..*B

7/5/14 8:56:33 PM :Debug: Real OchDelay for MyCar: 50, timeout=300
7/5/14 8:56:33 PM :Debug: commThreadExpectedReturnTime set to ms from now: 620
7/5/14 8:56:33 PM :Time: 0:04.998: SENT, 1 bytes
x4F                                                                   O

7/5/14 8:56:33 PM :Debug: old style time to read outpc: 49 ms.
7/5/14 8:56:33 PM :Time: 0:05.048: Received, 52 bytes
xB0 x04 x00 x00 x30 x76 x0E x42 x08 x71 x7F x42 x00 x00 x00 x00       ....0v.B.qB....
x1B xAA x21 x3F x08 x78 x10 x41 x00 x00 x00 x00 x01 x0A x20 x3D       ...?.x.A.......=
x5E x00 x00 x00 x77 x71 x37 x42 x00 x00 xC0 x7F x01 x00 x00 x00       ^...wq7B.......
xE6 xB4 x2A x42                                                       ..*B

7/5/14 8:56:33 PM :Debug: Real OchDelay for MyCar: 50, timeout=300
7/5/14 8:56:33 PM :Debug: commThreadExpectedReturnTime set to ms from now: 620
7/5/14 8:56:33 PM :Time: 0:05.065: SENT, 1 bytes
x4F                                                                   O

7/5/14 8:56:33 PM :Debug: old style time to read outpc: 50 ms.
7/5/14 8:56:33 PM :Time: 0:05.115: Received, 52 bytes
xB0 x04 x00 x00 xB0 x93 x1A x42 x60 x37 x7D x42 x00 x00 x00 x00       .......B`7}B....
x3F xEA x23 x3F x05 x54 x10 x41 x00 x00 x00 x00 x02 x0E xE0 x3C       ?.#?.T.A.......<
x61 x00 x00 x00 x93 x33 x39 x42 x00 x00 xC0 x7F x01 x00 x00 x00       a....39B.......
x9C x3C x33 x42                                                       .<3B

7/5/14 8:56:33 PM :Debug: Real OchDelay for MyCar: 50, timeout=300
7/5/14 8:56:33 PM :Debug: commThreadExpectedReturnTime set to ms from now: 620
7/5/14 8:56:33 PM :Time: 0:05.133: SENT, 1 bytes
x4F                                                                   O

Time: 0:05.141: Received Instruction: 
7/5/14 8:56:33 PM :Debug: old style time to read outpc: 49 ms.
7/5/14 8:56:33 PM :Time: 0:05.183: Received, 52 bytes
xB0 x04 x00 x00 xB0 x93 x1A x42 x60 x37 x7D x42 x00 x00 x00 x00       .......B`7}B....
x3F xEA x23 x3F x05 x54 x10 x41 x00 x00 x00 x00 x02 x0E xE0 x3C       ?.#?.T.A.......<
x61 x00 x00 x00 x93 x33 x39 x42 x00 x00 xC0 x7F x01 x00 x00 x00       a....39B.......
x9C x3C x33 x42                                                       .<3B

7/5/14 8:56:33 PM :Info: Initiating read page 1
7/5/14 8:56:33 PM :Info: Initiating read page 3
Time: 0:05.183: Received Instruction: 
7/5/14 8:56:33 PM :Debug: commThreadExpectedReturnTime set to ms from now: 860
Time: 0:05.207: Processing Instruction: 
7/5/14 8:56:33 PM :Time: 0:05.228: SENT, 3 bytes
x50 x00 x00                                                           P..

7/5/14 8:56:33 PM :Debug: commThreadExpectedReturnTime set to ms from now: 20140
7/5/14 8:56:33 PM :Time: 0:05.338: SENT, 7 bytes
x52 x00 x00 x00 x00 x64 x05                                           R....d.

7/5/14 8:56:33 PM :Debug: Read page time: 210ms.
7/5/14 8:56:33 PM :Time: 0:05.488: Received, 1380 bytes
x00 x00 x00 x00 x9A x99 xEF x42 x00 x00 x00 x41 x00 x00 x10 x41       .......B...A...A
x00 x00 x20 x41 x00 x00 x30 x41 x00 x00 x40 x41 x00 x00 x50 x41       ...A..0A..@A..PA
x00 x00 x60 x41 x00 x00 x70 x41 x00 x00 x00 x00 x00 x00 x00 x00       ..`A..pA........
x00 x00 x00 x00 x00 x00 x00 x00 x00 x00 x00 x00 x00 x00 x00 x00       ................
x00 x00 x00 x00 x00 x00 x00 x00 x00 x00 x20 xC2 x00 x00 xF0 xC1       ................
x00 x00 xA0 xC1 x00 x00 x20 xC1 x00 x00 x00 x00 x00 x00 x20 x41       ...............A
x00 x00 xA0 x41 x00 x00 xF0 x41 x00 x00 x20 x42 x00 x00 x48 x42       ...A...A...B..HB
x00 x00 x70 x42 x00 x00 x8C x42 x00 x00 xA0 x42 x00 x00 xB4 x42       ..pB...B...B...B
x00 x00 xC8 x42 x00 x00 xDC x42 x00 x00 x80 x3F x00 x00 x80 x3F       ...B...B...?...?
x00 x00 x80 x3F x00 x00 x80 x3F x00 x00 x80 x3F x00 x00 x80 x3F       ...?...?...?...?
x00 x00 x80 x3F x00 x00 x80 x3F x00 x00 x80 x3F x00 x00 x80 x3F       ...?...?...?...?
x00 x00 x80 x3F x00 x00 x80 x3F x00 x00 x80 x3F x00 x00 x80 x3F       ...?...?...?...?
x00 x00 x80 x3F x00 x00 x80 x3F x00 x00 x20 xC2 x00 x00 xF0 xC1       ...?...?........
x00 x00 xA0 xC1 x00 x00 x20 xC1 x00 x00 x00 x00 x00 x00 x20 x41       ...............A
x00 x00 xA0 x41 x00 x00 xF0 x41 x00 x00 x20 x42 x00 x00 x48 x42       ...A...A...B..HB
x00 x00 x70 x42 x00 x00 x8C x42 x00 x00 xA0 x42 x00 x00 xB4 x42       ..pB...B...B...B
x00 x00 xC8 x42 x00 x00 xDC x42 x00 x00 x80 x3F x00 x00 x80 x3F       ...B...B...?...?
x00 x00 x80 x3F x00 x00 x80 x3F x00 x00 x80 x3F x00 x00 x80 x3F       ...?...?...?...?
x00 x00 x80 x3F x00 x00 x80 x3F x00 x00 x80 x3F x00 x00 x80 x3F       ...?...?...?...?
x00 x00 x80 x3F x00 x00 x80 x3F x00 x00 x80 x3F x00 x00 x80 x3F       ...?...?...?...?
x00 x00 x80 x3F x00 x00 x80 x3F x00 x00 x64 x00 xEE x02 x01 x00       ...?...?..d.....
x00 x00 x00 x00 x00 x00 x82 x42 x00 x00 x70 x41 x00 x00 x00 x41       .......B..pA...A
x26 x02 x00 x00 x00 x00 x48 x44 xB8 xB6 xD2 x44 xB8 xB6 x20 x45       &.....HD...D...E
x3D x12 x58 x45 xCD xB6 x87 x45 x8F x64 xA3 x45 x3D x12 xBF x45       =.XE...E.d.E=..E
x00 xC0 xDA x45 x00 x00 x00 x00 x00 x00 x00 x00 x00 x00 x00 x00       ...E............
x00 x00 x00 x00 x00 x00 x00 x00 x00 x00 x00 x00 x00 x00 x00 x00       ................
x00 x00 x00 x00 x00 x00 x48 x44 xB8 xB6 xD2 x44 xB8 xB6 x20 x45       ......HD...D...E
x3D x12 x58 x45 xCD xB6 x87 x45 x8F x64 xA3 x45 x3D x12 xBF x45       =.XE...E.d.E=..E
x00 xC0 xDA x45 x00 x00 x00 x00 x00 x00 x00 x00 x00 x00 x00 x00       ...E............
x00 x00 x00 x00 x00 x00 x00 x00 x00 x00 x00 x00 x00 x00 x00 x00       ................
x00 x00 x00 x00 x00 x00 x00 x00 x00 x00 x00 x00 x01 x00 x00 x00       ................
x04 x00 x00 x00 x00 x00 xA0 xC1 x78 x1C xBF x41 x3C x8E x43 x42       ........x..A<.CB
x00 xA0 x8C x46 x00 x40 x03 x45 x00 x00 x7A x44 x00 x40 x4E x45       ...F.@.E..zD.@NE
x40 xB6 x5A xB9 x08 x13 x0C x3A x8C xA2 x99 xB5 x00 x00 x00 x42       @.Z....:.......B
x00 x00 x96 x42 x00 x00 xF0 x42 x00 x70 x14 x46 x00 x40 x03 x45       ...B...B.p.F.@.E
x00 x00 x7A x44 x00 xC0 x28 x45 x76 x1A x47 xBB xB4 xCE x7C x3A       ..zD..(Ev.G...|:
x0C xE7 x5B xB6 x00 x00 x00 x00 x00 x00 x00 x00 x00 x00 x00 x00       ..[.............
x00 x00 x00 x00 x00 x00 x00 x00 x00 x00 x80 x3F x00 xA0 x8C x45       ...........?...E
x00 x50 x43 x46 x00 x00 x80 xBF x00 x00 x80 xBF x00 x00 x80 xBF       .PCF............
x00 x00 x80 xBF x00 x00 x80 xBF x00 x00 x80 x40 x00 x00 x80 x40       ...........@...@
x00 x00 x00 x00 x99 x99 x99 x3F xE1 x7A xB4 x3F x29 x5C xCF x3F       .......?.z.?)\.?
x1E x85 xEB x3F x33 x33 x03 x40 xD7 xA3 x10 x40 x52 xB8 x1E x40       ...?33.@...@R..@
xF6 x28 x2C x40 x99 x99 x39 x40 x14 xAE x47 x40 xB8 x1E x55 x40       .(,@..9@..G@..U@
x5C x8F x62 x40 xD7 xA3 x70 x40 x7B x14 x7E x40 x8F xC2 x85 x40       \.b@..p@{.~@...@
xCD xCC x8C x40 x00 x00 x48 x44 x8F xAA x97 x44 x1E x55 xCB x44       ...@..HD...D.U.D
x00 x00 xFF x44 x47 x55 x19 x45 x8F x2A x33 x45 x00 x00 x4D x45       ...DGU.E.*3E..ME
x47 xD5 x66 x45 x47 x55 x80 x45 x00 x40 x8D x45 xA4 x2A x9A x45       G.fEGU.E.@.E.*.E
x47 x15 xA7 x45 x00 x00 xB4 x45 xA4 xEA xC0 x45 x47 xD5 xCD x45       G..E...E...EG..E
x00 xC0 xDA x45 x00 x00 xAE x42 x00 x00 x8C x42 x00 x00 x00 x00       ...E...B...B....
x00 x00 x48 x42 x03 x00 x00 x00 x99 x99 x99 x3F xE1 x7A xB4 x3F       ..HB.......?.z.?
x29 x5C xCF x3F x1E x85 xEB x3F x33 x33 x03 x40 xD7 xA3 x10 x40       )\.?...?33.@...@
x52 xB8 x1E x40 xF6 x28 x2C x40 x99 x99 x39 x40 x14 xAE x47 x40       R..@.(,@..9@..G@
xB8 x1E x55 x40 x5C x8F x62 x40 xD7 xA3 x70 x40 x7B x14 x7E x40       ..U@\.b@..p@{.~@
x8F xC2 x85 x40 xCD xCC x8C x40 x00 x00 x48 x44 x8F xAA x97 x44       ...@...@..HD...D
x1E x55 xCB x44 x00 x00 xFF x44 x47 x55 x19 x45 x8F x2A x33 x45       .U.D...DGU.E.*3E
x00 x00 x4D x45 x47 xD5 x66 x45 x47 x55 x80 x45 x00 x40 x8D x45       ..MEG.fEGU.E.@.E
xA4 x2A x9A x45 x47 x15 xA7 x45 x00 x00 xB4 x45 xA4 xEA xC0 x45       .*.EG..E...E...E
x47 xD5 xCD x45 x00 xC0 xDA x45 x66 x66 xA6 x3F x58 x1B x00 x00       G..E...Eff.?X...
x00 x00 x00 x00 x01 x00 x00 x00 x00 x00 x2F x43 x00 x00 x00 x40       ........../C...@
x00 x00 x00 x00 xAB xAA xAA x40 x00 x00 x96 x42 x00 x00 x8C x42       .......@...B...B
x01 x00 x00 x00 x00 x00 x00 x00 x00 x00 x00 x00 x32 x00 x00 x00       ............2...
x04 x00 x00 x00 x00 x00 x00 x00 x01 x00 x00 x00 x00 x00 x00 x3F       ...............?
x01 x00 x00 x00 x00 x00 x00 x00 xA1 x52 x33 x01 x14 x00 x00 x00       .........R3.....
x04 x00 x00 x00 x03 x00 x00 x00 x01 x00 x00 x00 x14 x00 x00 x00       ................
x01 x00 x00 x00 x00 x00 x00 x00 x00 x00 x00 x00 x00 x00 x00 x00       ................
x00 x00 xC0 x3F x00 x00 x20 x40 x01 x00 x00 x00 x01 x00 x00 x00       ...?...@........
x00 x00 x00 x00 x00 x00 x80 x3F x0B x00 x00 x00 x07 x00 x00 x00       .......?........
x01 x00 x00 x00 x0E x00 x00 x00 x00 x00 x00 x00 x00 x00 x10 x41       ...............A
x00 x00 xA0 x40 x00 x00 x98 x41 x00 x00 x6C x42 x00 x00 x14 x42       ...@...A..lB...B
x00 x00 x80 x3F x00 x00 x00 x00 x00 x00 xFA x43 x00 x00 x00 x00       ...?.......C....
x04 x00 x00 x00 x00 x00 x00 x00 x00 x00 x00 x00 x00 x00 x00 x00       ................
x00 x00 x00 x00 x00 x00 x00 x00 x00 x00 x00 x00 x00 x00 x00 x00       ................
x00 x00 x00 x00 x00 x00 x00 x00 x00 x00 x00 x00 x00 x00 x00 x00       ................
x00 x00 x00 x00 x00 x00 x00 x00 x00 x00 x00 x00 x00 x00 x00 x00       ................
x00 x00 x00 x00 x00 x00 x00 x00 x00 x00 x00 x00 x00 x00 x00 x00       ................
x00 x00 x00 x00 x00 x00 x00 x00 x00 x00 x00 x00 x00 x00 x00 x00       ................
x00 x00 x00 x00 x00 x00 x00 x00 x00 x00 x00 x00 x00 x00 x00 x00       ................
x00 x00 x00 x00 x00 x00 x00 x00 x00 x00 x00 x00 x00 x00 x00 x00       ................
x00 x00 x00 x00 x00 x00 x00 x00 x00 x00 x00 x00 x00 x00 x00 x00       ................
x00 x00 x00 x00 x00 x00 x00 x00 x00 x00 x00 x00 x00 x00 x00 x00       ................
x00 x00 x00 x00 x00 x00 x00 x00 x00 x00 x00 x00 x00 x00 x00 x00       ................
x00 x00 x00 x00 x00 x00 x00 x00 x00 x00 x00 x00 x00 x00 x00 x00       ................
x00 x00 x00 x00 x00 x00 x00 x00 x00 x00 x00 x00 x00 x00 x00 x00       ................
x00 x00 x00 x00 x00 x00 x00 x00 x00 x00 x00 x00 x00 x00 x00 x00       ................
x00 x00 x00 x00 x00 x00 x00 x00 x00 x00 x00 x00 x00 x00 x00 x00       ................
x00 x00 x00 x00 x00 x00 x00 x00 x00 x00 x00 x00 x00 x00 x00 x00       ................
x00 x00 x00 x00                                                       ....

Time: 0:05.489: Processing Complete: 
7/5/14 8:56:33 PM :Debug: commThreadExpectedReturnTime set to ms from now: 860
Time: 0:05.514: Processing Instruction: 
7/5/14 8:56:33 PM :Time: 0:05.535: SENT, 3 bytes
x50 x02 x00                                                           P..

7/5/14 8:56:33 PM :Debug: commThreadExpectedReturnTime set to ms from now: 20140
7/5/14 8:56:34 PM :Time: 0:05.645: SENT, 7 bytes
x52 x02 x00 x00 x00 x00 x04                                           R......

7/5/14 8:56:34 PM :Debug: Read page time: 210ms.
7/5/14 8:56:34 PM :Time: 0:05.795: Received, 1024 bytes
x42 x60 xC5 x3F xC2 x17 xC6 x3F x94 xA3 xC6 x3F xC3 xF5 xC8 x3F       B`.?...?...?...?
x66 x66 xC6 x3F x56 x9E x68 x3F x03 x78 x4B x3F x82 x73 x46 x3F       ff.?V.h?.xK?.sF?
x04 xAF x4A x3F xCD xCC x4C x3F x71 x75 x4C x3F x85 x44 x4E x3F       ..J?..L?quL?.DN?
x29 x5C x4F x3F x29 x5C x4F x3F x29 x5C x4F x3F x29 x5C x4F x3F       )\O?)\O?)\O?)\O?
xEF x1C xC4 x3F x92 x5C xC8 x3F x2A x8F xC6 x3F x44 xC1 xC6 x3F       ...?.\.?*..?D..?
xEB xE3 xC5 x3F xB4 x55 x4D x3F x29 x5C x4F x3F x98 xDB x49 x3F       ...?.UM?)\O?..I?
xF0 x13 x4F x3F x78 xB7 x3E x3F x82 x8D x33 x3F x93 x1E x36 x3F       ..O?x.>?..3?..6?
x7F xA2 x3E x3F x29 x5C x4F x3F x29 x5C x4F x3F x29 x5C x4F x3F       .>?)\O?)\O?)\O?
xAF x94 xC5 x3F x56 xD5 xC5 x3F x91 x29 xC7 x3F x71 xE2 xC5 x3F       ...?V..?.).?q..?
xA2 x29 xB5 x3F x1D x1C xEC x3D x00 x00 x00 x00 x00 x00 x00 x00       .).?...=........
x00 x00 x00 x00 x00 x00 x00 x00 x00 x00 x00 x00 x00 x00 x00 x00       ................
x00 x00 x00 x00 x00 x00 x00 x00 x00 x00 x00 x00 x00 x00 x00 x00       ................
x66 xF7 xC4 x3F x5A xF6 xDE x3F x81 x7A xC7 x3F x4E xB4 xCB x3F       f..?Z..?.z.?N..?
x6F x48 x9D x3F x00 x00 x00 x00 x00 x00 x00 x00 x00 x00 x00 x00       oH.?............
x00 x00 x00 x00 x00 x00 x00 x00 x00 x00 x00 x00 x00 x00 x00 x00       ................
x00 x00 x00 x00 x00 x00 x00 x00 x00 x00 x00 x00 x00 x00 x00 x00       ................
xEF xAA x14 x40 xC8 x27 x5C x40 xAE x62 x34 x40 x49 x81 x0F x40       ...@.'\@.b4@I..@
xBF x0D x08 x40 x56 xD6 x98 x3F xD6 x58 xFA x3E x00 x00 x00 x00       ...@V..?.X.>....
x00 x00 x00 x00 x00 x00 x00 x00 x00 x00 x00 x00 x00 x00 x00 x00       ................
x00 x00 x00 x00 x00 x00 x00 x00 x00 x00 x00 x00 x00 x00 x00 x00       ................
x19 x4B xF6 x40 xEC xA3 xBE x40 x69 x6E x96 x40 xD0 x44 x78 x40       .K.@...@in.@.Dx@
xD9 x5F x46 x40 x92 xCC x19 x40 xC9 x5A x1D x40 xCD x3E xE5 x3F       ._F@...@.Z.@.>.?
xB1 x31 x0C x40 x58 xC7 x04 x40 xB0 x37 xAF x3F xA3 xCE xA4 x3F       .1.@X..@.7.?...?
x00 x00 x00 x00 x00 x00 x00 x00 x00 x00 x00 x00 x00 x00 x00 x00       ................
xAF x47 x65 x41 x54 x5F x0B x41 x3C xDC xD1 x40 x88 xBA xAF x40       .GeAT_.A<..@...@
x83 xC2 xA3 x40 xAC xE1 x89 x40 x93 xDF x4B x40 xB2 xBA x55 x40       ...@...@..K@..U@
x59 x86 x38 x40 x19 xC9 x35 x40 x62 x2C x29 x40 x6D x53 x20 x40       Y.8@..5@b,)@mS.@
x26 xFC x12 x40 x00 x00 x00 x00 x00 x00 x00 x00 x00 x00 x00 x00       &..@............
x00 xD5 xAA x41 xDC xA7 x76 x41 x02 x41 x2F x41 xEA x78 x0C x41       ...A..vA.A/A.x.A
x36 xBA xBB x40 x06 x3C xA1 x40 xC7 x9F xA3 x40 x78 xA8 x8C x40       6..@.<.@...@x..@
xBE x30 x91 x40 xFB xCC x63 x40 x25 x08 x75 x40 x11 x6F x49 x40       .0.@..c@%.u@.oI@
x56 x2C x58 x40 x85 xEB x31 x40 x85 xEB x31 x40 x85 xEB x31 x40       V,X@..1@..1@..1@
xC8 x29 xA0 x41 x57 x7D x82 x41 x06 xAE x89 x41 x93 x9B x79 x41       .).AW}.A...A..yA
xF3 x33 x2F x41 x3A xC0 xF8 x40 xB8 xC8 xC7 x40 xD2 xD1 xEC x40       .3/A:..@...@...@
x62 x81 xD5 x40 x49 x49 xC4 x40 xC0 xF5 xB0 x40 x77 x9F x98 x40       b..@II.@...@w..@
x79 xE6 x90 x40 xEC x51 x80 x40 xEC x51 x80 x40 xEC x51 x80 x40       y..@.Q.@.Q.@.Q.@
xAC x1C x92 x41 x18 x6D x77 x41 x0D x86 x79 x41 x08 x55 x76 x41       ...A.mwA..yA.UvA
xED xCA x4F x41 x5C x6D x55 x41 xE4 x5C x0E x41 x5B xD6 x0E x41       ..OA\mUA.\.A[..A
xAD x86 x00 x41 xFA x9B xD8 x40 xC3 x58 xBA x40 x7E x38 xCD x40       ...A...@.X.@~8.@
x64 xDB xC2 x40 x29 x5C xB7 x40 x29 x5C xB7 x40 x29 x5C xB7 x40       d..@)\.@)\.@)\.@
x3D x51 x8B x41 xC7 xDC x75 x41 x80 xFF x72 x41 x17 x6A x75 x41       =Q.A..uA..rA.juA
xEE xE7 x74 x41 xB3 x30 x76 x41 x66 x88 x67 x41 x57 x11 x3F x41       ..tA.0vAf.gAW.?A
xD7 xC4 x2F x41 x6A x4D x1F x41 x47 x4E x10 x41 x9C x10 x07 x41       ../AjM.AGN.A...A
x83 x7C xF0 x40 xCD xCC xDC x40 xCD xCC xDC x40 xCD xCC xDC x40       .|.@...@...@...@
xEC x0A x88 x41 xF3 xF4 x75 x41 xB4 x02 x73 x41 xC9 x73 x74 x41       ...A..uA..sA.stA
xCA x36 x75 x41 x7F xFC x78 x41 xF5 x38 x7A x41 xA5 xA5 x76 x41       .6uA.xA.8zA..vA
x17 x16 x5A x41 x4C xB3 x2E x41 x0E x22 x38 x41 x67 x8F x2A x41       ..ZAL..A."8Ag.*A
x3D xD4 x18 x41 x14 xAE x13 x41 x14 xAE x13 x41 x14 xAE x13 x41       =..A...A...A...A
x95 xD4 x87 x41 xFA xC3 x75 x41 xB9 xBA x72 x41 xAE xD3 x74 x41       ...A..uA..rA..tA
xE8 x4D x75 x41 x4E xF3 x7A x41 xBA xF7 x7C x41 x40 x3D x7B x41       .MuAN.zA..|A@={A
xED x3F x7D x41 xE4 xD6 x71 x41 xF1 xA7 x6A x41 xA3 x8A x3E x41       .?}A..qA..jA..>A
x61 xBF x40 x41 x14 xAE x13 x41 x14 xAE x13 x41 x14 xAE x13 x41       a.@A...A...A...A
x07 xCE x87 x41 x46 x7D x75 x41 x35 xE4 x74 x41 x42 x98 x74 x41       ...AF}uA5.tAB.tA
xEE x9E x74 x41 xD4 xBE x77 x41 x96 xDC x7E x41 x61 x7C x7C x41       ..tA..wA..~Aa||A
x64 xB4 x7A x41 x18 x63 x7D x41 x97 xFC x80 x41 xF2 xDF x70 x41       d.zA.c}A...A..pA
xB7 x8F x6F x41 x8F xC2 x69 x41 x8F xC2 x69 x41 x8F xC2 x69 x41       ..oA..iA..iA..iA
xE8 xB1 x87 x41 xEE xE4 x75 x41 x96 x5D x73 x41 x77 xA6 x74 x41       ...A..uA.]sAw.tA
x25 x38 x74 x41 xBF xC5 x77 x41 xC2 x3C x7D x41 xC6 xD6 x7C x41       %8tA..wA.<}A..|A
x9E xD8 x7A x41 xE2 x3B x7D x41 x59 xF4 x7F x41 x41 x38 x80 x41       ..zA.;}AY.AA8.A
xDB xA7 x77 x41 x3D x0A x73 x41 x3D x0A x73 x41 x3D x0A x73 x41       ..wA=.sA=.sA=.sA
x7B x14 x88 x41 x00 x00 x74 x41 x48 xE1 x7A x41 x3D x0A x77 x41       {..A..tAH.zA=.wA
xEC x51 x74 x41 x1F x85 x77 x41 xCD xCC x7C x41 x14 xAE x7B x41       .QtA..wA..|A..{A
x9A x99 x79 x41 xD7 xA3 x7C x41 xC3 xF5 x80 x41 x48 xE1 x80 x41       ..yA..|A...AH..A
x7B x14 x7A x41 x66 x66 x72 x41 x66 x66 x72 x41 x66 x66 x72 x41       {.zAffrAffrAffrA

Time: 0:05.796: Processing Complete: 
7/5/14 8:56:34 PM :Debug: Real OchDelay for MyCar: 50, timeout=300
7/5/14 8:56:34 PM :Debug: commThreadExpectedReturnTime set to ms from now: 620
7/5/14 8:56:34 PM :Time: 0:05.846: SENT, 1 bytes
x4F                                                                   O

7/5/14 8:56:34 PM :Debug: old style time to read outpc: 49 ms.
7/5/14 8:56:34 PM :Time: 0:05.896: Received, 52 bytes
xB0 x04 x00 x00 xB0 x93 x1A x42 x60 x37 x7D x42 x00 x00 x00 x00       .......B`7}B....
x81 x0A x28 x3F x05 x48 x10 x41 x00 x00 x00 x00 x02 x0C xC0 x3C       ..(?.H.A.......<
x4B x00 x00 x00 x93 x33 x39 x42 x00 x00 xC0 x7F x01 x00 x00 x00       K....39B.......
x9C x3C x33 x42                                                       .<3B

7/5/14 8:56:34 PM :Debug: Real OchDelay for MyCar: 50, timeout=300
7/5/14 8:56:34 PM :Debug: commThreadExpectedReturnTime set to ms from now: 620
7/5/14 8:56:34 PM :Time: 0:05.912: SENT, 1 bytes
x4F                                                                   O

7/5/14 8:56:34 PM :Debug: old style time to read outpc: 49 ms.
7/5/14 8:56:34 PM :Time: 0:05.962: Received, 52 bytes
xB0 x04 x00 x00 xB0 x93 x1A x42 x60 x37 x7D x42 x00 x00 x00 x00       .......B`7}B....
x81 x0A x28 x3F x05 x48 x10 x41 x00 x00 x00 x00 x02 x0C xC0 x3C       ..(?.H.A.......<
x4B x00 x00 x00 x93 x33 x39 x42 x00 x00 xC0 x7F x01 x00 x00 x00       K....39B.......
x9C x3C x33 x42                                                       .<3B

7/5/14 8:56:34 PM :Debug: Real OchDelay for MyCar: 50, timeout=300
7/5/14 8:56:34 PM :Debug: commThreadExpectedReturnTime set to ms from now: 620
7/5/14 8:56:34 PM :Time: 0:05.982: SENT, 1 bytes
x4F                                                                   O

7/5/14 8:56:34 PM :Debug: old style time to read outpc: 49 ms.
7/5/14 8:56:34 PM :Time: 0:06.032: Received, 52 bytes
xB0 x04 x00 x00 xA0 x54 x10 x42 xF8 x95 x7D x42 x00 x00 x00 x00       .....T.B..}B....
x87 x6A x28 x3F x05 x48 x10 x41 x00 x00 x00 x00 x02 x0C xC0 x3C       .j(?.H.A.......<
x4E x00 x00 x00 x8A x9D x38 x42 x00 x00 xC0 x7F x01 x00 x00 x00       N.....8B.......
xF6 xA4 x2B x42                                                       ..+B

7/5/14 8:56:34 PM :Debug: Real OchDelay for MyCar: 50, timeout=300
7/5/14 8:56:34 PM :Debug: commThreadExpectedReturnTime set to ms from now: 620
7/5/14 8:56:34 PM :Time: 0:06.048: SENT, 1 bytes
x4F                                                                   O

7/5/14 8:56:34 PM :Debug: old style time to read outpc: 49 ms.
7/5/14 8:56:34 PM :Time: 0:06.098: Received, 52 bytes
xB0 x04 x00 x00 xA0 x54 x10 x42 xF8 x95 x7D x42 x00 x00 x00 x00       .....T.B..}B....
x87 x6A x28 x3F x05 x48 x10 x41 x00 x00 x00 x00 x02 x0C xC0 x3C       .j(?.H.A.......<
x4E x00 x00 x00 x8A x9D x38 x42 x00 x00 xC0 x7F x01 x00 x00 x00       N.....8B.......
xF6 xA4 x2B x42                                                       ..+B

7/5/14 8:56:34 PM :Debug: Real OchDelay for MyCar: 50, timeout=300
7/5/14 8:56:34 PM :Debug: commThreadExpectedReturnTime set to ms from now: 620
7/5/14 8:56:34 PM :Time: 0:06.114: SENT, 1 bytes
x4F                                                                   O

7/5/14 8:56:34 PM :Debug: old style time to read outpc: 49 ms.
7/5/14 8:56:34 PM :Time: 0:06.164: Received, 52 bytes
xB0 x04 x00 x00 xA0 x54 x10 x42 xF8 x95 x7D x42 x00 x00 x00 x00       .....T.B..}B....
x87 x6A x28 x3F x05 x48 x10 x41 x00 x00 x00 x00 x02 x0C xC0 x3C       .j(?.H.A.......<
x4E x00 x00 x00 x8A x9D x38 x42 x00 x00 xC0 x7F x01 x00 x00 x00       N.....8B.......
xF6 xA4 x2B x42                                                       ..+B

7/5/14 8:56:34 PM :Debug: Real OchDelay for MyCar: 50, timeout=300
7/5/14 8:56:34 PM :Debug: commThreadExpectedReturnTime set to ms from now: 620
7/5/14 8:56:34 PM :Time: 0:06.180: SENT, 1 bytes
x4F                                                                   O

7/5/14 8:56:34 PM :Debug: old style time to read outpc: 49 ms.
7/5/14 8:56:34 PM :Time: 0:06.230: Received, 52 bytes
xB0 x04 x00 x00 xA0 x54 x10 x42 xF8 x95 x7D x42 x00 x00 x00 x00       .....T.B..}B....
x87 x6A x28 x3F x05 x48 x10 x41 x00 x00 x00 x00 x02 x0C xC0 x3C       .j(?.H.A.......<
x4E x00 x00 x00 x8A x9D x38 x42 x00 x00 xC0 x7F x01 x00 x00 x00       N.....8B.......
xF6 xA4 x2B x42                                                       ..+B

7/5/14 8:56:34 PM :Debug: Real OchDelay for MyCar: 50, timeout=300
7/5/14 8:56:34 PM :Debug: commThreadExpectedReturnTime set to ms from now: 620
7/5/14 8:56:34 PM :Time: 0:06.246: SENT, 1 bytes
x4F                                                                   O

7/5/14 8:56:34 PM :Time: 0:06.296: Received, 52 bytes
xB0 x04 x00 x00 xA0 x54 x10 x42 xF8 x95 x7D x42 x00 x00 x00 x00       .....T.B..}B....
x0F xEA x20 x3F x06 x60 x10 x41 x00 x00 x00 x00 x01 x08 x00 x3D       ...?.`.A.......=
x60 x00 x00 x00 x93 x33 x39 x42 x00 x00 xC0 x7F x01 x00 x00 x00       `....39B.......
xF6 xA4 x2B x42                                                       ..+B

7/5/14 8:56:34 PM :Debug: old style time to read outpc: 49 ms.
7/5/14 8:56:34 PM :Debug: Real OchDelay for MyCar: 50, timeout=300
7/5/14 8:56:34 PM :Debug: commThreadExpectedReturnTime set to ms from now: 620
7/5/14 8:56:34 PM :Time: 0:06.312: SENT, 1 bytes
x4F                                                                   O

7/5/14 8:56:34 PM :Debug: old style time to read outpc: 50 ms.
7/5/14 8:56:34 PM :Time: 0:06.362: Received, 52 bytes
xB0 x04 x00 x00 xA0 x54 x10 x42 xF8 x95 x7D x42 x00 x00 x00 x00       .....T.B..}B....
x0F xEA x20 x3F x06 x60 x10 x41 x00 x00 x00 x00 x01 x08 x00 x3D       ...?.`.A.......=
x60 x00 x00 x00 x93 x33 x39 x42 x00 x00 xC0 x7F x01 x00 x00 x00       `....39B.......
xF6 xA4 x2B x42                                                       ..+B

7/5/14 8:56:34 PM :Debug: Real OchDelay for MyCar: 50, timeout=300
7/5/14 8:56:34 PM :Debug: commThreadExpectedReturnTime set to ms from now: 620
7/5/14 8:56:34 PM :Time: 0:06.378: SENT, 1 bytes
x4F                                                                   O

7/5/14 8:56:34 PM :Debug: old style time to read outpc: 49 ms.
7/5/14 8:56:34 PM :Time: 0:06.428: Received, 52 bytes
xB0 x04 x00 x00 xA0 x54 x10 x42 xF8 x95 x7D x42 x00 x00 x00 x00       .....T.B..}B....
x0F xEA x20 x3F x06 x60 x10 x41 x00 x00 x00 x00 x01 x08 x00 x3D       ...?.`.A.......=
x60 x00 x00 x00 x93 x33 x39 x42 x00 x00 xC0 x7F x01 x00 x00 x00       `....39B.......
xF6 xA4 x2B x42                                                       ..+B

7/5/14 8:56:34 PM :Debug: Real OchDelay for MyCar: 50, timeout=300
7/5/14 8:56:34 PM :Debug: commThreadExpectedReturnTime set to ms from now: 620
7/5/14 8:56:34 PM :Time: 0:06.444: SENT, 1 bytes
x4F                                                                   O

7/5/14 8:56:34 PM :Debug: old style time to read outpc: 49 ms.
7/5/14 8:56:34 PM :Time: 0:06.494: Received, 52 bytes
xB0 x04 x00 x00 xA0 x54 x10 x42 xF8 x95 x7D x42 x00 x00 x00 x00       .....T.B..}B....
x0F xEA x20 x3F x06 x60 x10 x41 x00 x00 x00 x00 x01 x08 x00 x3D       ...?.`.A.......=
x60 x00 x00 x00 x93 x33 x39 x42 x00 x00 xC0 x7F x01 x00 x00 x00       `....39B.......
xF6 xA4 x2B x42                                                       ..+B

7/5/14 8:56:34 PM :Debug: Real OchDelay for MyCar: 50, timeout=300
7/5/14 8:56:34 PM :Debug: commThreadExpectedReturnTime set to ms from now: 620
7/5/14 8:56:34 PM :Time: 0:06.510: SENT, 1 bytes
x4F                                                                   O

7/5/14 8:56:34 PM :Debug: old style time to read outpc: 49 ms.
7/5/14 8:56:34 PM :Time: 0:06.560: Received, 52 bytes
xB0 x04 x00 x00 xA0 x54 x10 x42 xF8 x95 x7D x42 x00 x00 x00 x00       .....T.B..}B....
x0F xEA x20 x3F x06 x60 x10 x41 x00 x00 x00 x00 x01 x08 x00 x3D       ...?.`.A.......=
x60 x00 x00 x00 x93 x33 x39 x42 x00 x00 xC0 x7F x01 x00 x00 x00       `....39B.......
xF6 xA4 x2B x42                                                       ..+B

7/5/14 8:56:34 PM :Debug: Real OchDelay for MyCar: 50, timeout=300
7/5/14 8:56:34 PM :Debug: commThreadExpectedReturnTime set to ms from now: 620
7/5/14 8:56:34 PM :Time: 0:06.576: SENT, 1 bytes
x4F                                                                   O

7/5/14 8:56:35 PM :Debug: old style time to read outpc: 49 ms.
7/5/14 8:56:35 PM :Time: 0:06.626: Received, 52 bytes
xAF x04 x00 x00 xB8 x45 x11 x42 x18 xE2 x7E x42 x00 x00 x00 x00       .....E.B..~B....
x45 x4A x24 x3F x05 x54 x10 x41 x00 x00 x00 x00 x02 x0E xE0 x3C       EJ$?.T.A.......<
x55 x00 x00 x00 x93 x33 x39 x42 x00 x00 xC0 x7F x01 x00 x00 x00       U....39B.......
xD0 xAC x2C x42                                                       ..,B

7/5/14 8:56:35 PM :Debug: Real OchDelay for MyCar: 50, timeout=300
7/5/14 8:56:35 PM :Debug: commThreadExpectedReturnTime set to ms from now: 620
7/5/14 8:56:35 PM :Time: 0:06.642: SENT, 1 bytes
x4F                                                                   O

7/5/14 8:56:35 PM :Debug: old style time to read outpc: 49 ms.
7/5/14 8:56:35 PM :Time: 0:06.692: Received, 52 bytes
xAF x04 x00 x00 xB8 x45 x11 x42 x18 xE2 x7E x42 x00 x00 x00 x00       .....E.B..~B....
x45 x4A x24 x3F x05 x54 x10 x41 x00 x00 x00 x00 x02 x0E xE0 x3C       EJ$?.T.A.......<
x55 x00 x00 x00 x93 x33 x39 x42 x00 x00 xC0 x7F x01 x00 x00 x00       U....39B.......
xD0 xAC x2C x42                                                       ..,B

7/5/14 8:56:35 PM :Debug: Real OchDelay for MyCar: 50, timeout=300
7/5/14 8:56:35 PM :Debug: commThreadExpectedReturnTime set to ms from now: 620
7/5/14 8:56:35 PM :Time: 0:06.708: SENT, 1 bytes
x4F                                                                   O

7/5/14 8:56:35 PM :Debug: old style time to read outpc: 49 ms.
7/5/14 8:56:35 PM :Time: 0:06.758: Received, 52 bytes
xAF x04 x00 x00 xB8 x45 x11 x42 x18 xE2 x7E x42 x00 x00 x00 x00       .....E.B..~B....
x45 x4A x24 x3F x05 x54 x10 x41 x00 x00 x00 x00 x02 x0E xE0 x3C       EJ$?.T.A.......<
x55 x00 x00 x00 x93 x33 x39 x42 x00 x00 xC0 x7F x01 x00 x00 x00       U....39B.......
xD0 xAC x2C x42                                                       ..,B

7/5/14 8:56:35 PM :Debug: Real OchDelay for MyCar: 50, timeout=300
7/5/14 8:56:35 PM :Debug: commThreadExpectedReturnTime set to ms from now: 620
7/5/14 8:56:35 PM :Time: 0:06.774: SENT, 1 bytes
x4F                                                                   O

7/5/14 8:56:35 PM :Debug: old style time to read outpc: 49 ms.
7/5/14 8:56:35 PM :Time: 0:06.824: Received, 52 bytes
xAF x04 x00 x00 xB8 x45 x11 x42 x18 xE2 x7E x42 x00 x00 x00 x00       .....E.B..~B....
x45 x4A x24 x3F x05 x54 x10 x41 x00 x00 x00 x00 x02 x0E xE0 x3C       EJ$?.T.A.......<
x55 x00 x00 x00 x93 x33 x39 x42 x00 x00 xC0 x7F x01 x00 x00 x00       U....39B.......
xD0 xAC x2C x42                                                       ..,B

7/5/14 8:56:35 PM :Debug: Real OchDelay for MyCar: 50, timeout=300
7/5/14 8:56:35 PM :Debug: commThreadExpectedReturnTime set to ms from now: 620
7/5/14 8:56:35 PM :Time: 0:06.841: SENT, 1 bytes
x4F                                                                   O

7/5/14 8:56:35 PM :Debug: old style time to read outpc: 50 ms.
7/5/14 8:56:35 PM :Time: 0:06.891: Received, 52 bytes
xB0 x04 x00 x00 x88 xF4 x0F x42 x88 xB2 x7E x42 x00 x00 x00 x00       .......B..~B....
x2D xCA x22 x3F x00 x00 x10 x41 x00 x00 x00 x00 x00 x00 x00 x00       -."?...A........
x4D x00 x00 x00 x29 x94 x42 x42 x00 x00 xC0 x7F x01 x00 x00 x00       M...).BB.......
x08 xA4 x2B x42                                                       ..+B

7/5/14 8:56:35 PM :Debug: Real OchDelay for MyCar: 50, timeout=300
7/5/14 8:56:35 PM :Debug: commThreadExpectedReturnTime set to ms from now: 620
7/5/14 8:56:35 PM :Time: 0:06.908: SENT, 1 bytes
x4F                                                                   O

7/5/14 8:56:35 PM :Debug: old style time to read outpc: 49 ms.
7/5/14 8:56:35 PM :Time: 0:06.958: Received, 52 bytes
xB0 x04 x00 x00 x88 xF4 x0F x42 x88 xB2 x7E x42 x00 x00 x00 x00       .......B..~B....
x2D xCA x22 x3F x00 x00 x10 x41 x00 x00 x00 x00 x00 x00 x00 x00       -."?...A........
x4D x00 x00 x00 x29 x94 x42 x42 x00 x00 xC0 x7F x01 x00 x00 x00       M...).BB.......
x08 xA4 x2B x42                                                       ..+B

7/5/14 8:56:35 PM :Debug: Real OchDelay for MyCar: 50, timeout=300
7/5/14 8:56:35 PM :Debug: commThreadExpectedReturnTime set to ms from now: 620
7/5/14 8:56:35 PM :Time: 0:06.974: SENT, 1 bytes
x4F                                                                   O

7/5/14 8:56:35 PM :Time: 0:07.024: Received, 52 bytes
xB0 x04 x00 x00 x88 xF4 x0F x42 x88 xB2 x7E x42 x00 x00 x00 x00       .......B..~B....
x2D xCA x22 x3F x00 x00 x10 x41 x00 x00 x00 x00 x00 x00 x00 x00       -."?...A........
x4D x00 x00 x00 x29 x94 x42 x42 x00 x00 xC0 x7F x01 x00 x00 x00       M...).BB.......
x08 xA4 x2B x42                                                       ..+B

7/5/14 8:56:35 PM :Debug: old style time to read outpc: 49 ms.
7/5/14 8:56:35 PM :Debug: Real OchDelay for MyCar: 50, timeout=300
7/5/14 8:56:35 PM :Debug: commThreadExpectedReturnTime set to ms from now: 620
7/5/14 8:56:35 PM :Time: 0:07.040: SENT, 1 bytes
x4F                                                                   O

7/5/14 8:56:35 PM :Time: 0:07.091: Received, 52 bytes
xB0 x04 x00 x00 x88 xF4 x0F x42 x88 xB2 x7E x42 x00 x00 x00 x00       .......B..~B....
x2D xCA x22 x3F x00 x00 x10 x41 x00 x00 x00 x00 x00 x00 x00 x00       -."?...A........
x4D x00 x00 x00 x29 x94 x42 x42 x00 x00 xC0 x7F x01 x00 x00 x00       M...).BB.......
x08 xA4 x2B x42                                                       ..+B

7/5/14 8:56:35 PM :Debug: old style time to read outpc: 50 ms.
7/5/14 8:56:35 PM :Debug: Real OchDelay for MyCar: 50, timeout=300
7/5/14 8:56:35 PM :Debug: commThreadExpectedReturnTime set to ms from now: 620
7/5/14 8:56:35 PM :Time: 0:07.107: SENT, 1 bytes
x4F                                                                   O

7/5/14 8:56:35 PM :Time: 0:07.157: Received, 52 bytes
xB0 x04 x00 x00 x88 xF4 x0F x42 x88 xB2 x7E x42 x00 x00 x00 x00       .......B..~B....
x2D xCA x22 x3F x00 x00 x10 x41 x00 x00 x00 x00 x00 x00 x00 x00       -."?...A........
x4D x00 x00 x00 x29 x94 x42 x42 x00 x00 xC0 x7F x01 x00 x00 x00       M...).BB.......
x08 xA4 x2B x42                                                       ..+B

7/5/14 8:56:35 PM :Debug: old style time to read outpc: 49 ms.
7/5/14 8:56:35 PM :Debug: Real OchDelay for MyCar: 50, timeout=300
7/5/14 8:56:35 PM :Debug: commThreadExpectedReturnTime set to ms from now: 620
7/5/14 8:56:35 PM :Time: 0:07.173: SENT, 1 bytes
x4F                                                                   O

7/5/14 8:56:35 PM :Debug: old style time to read outpc: 49 ms.
7/5/14 8:56:35 PM :Time: 0:07.223: Received, 52 bytes
xB0 x04 x00 x00 x30 x93 x1B x42 x90 x53 x7E x42 x00 x00 x00 x00       ....0..B.S~B....
x09 x8A x20 x3F x03 x30 x10 x41 x00 x00 x00 x00 x01 x08 x80 x3C       ...?.0.A.......<
x57 x00 x00 x00 x93 x33 x39 x42 x00 x00 xC0 x7F x01 x00 x00 x00       W....39B.......
x48 x43 x34 x42                                                       HC4B

7/5/14 8:56:35 PM :Debug: Real OchDelay for MyCar: 50, timeout=300
7/5/14 8:56:35 PM :Debug: commThreadExpectedReturnTime set to ms from now: 620
7/5/14 8:56:35 PM :Time: 0:07.239: SENT, 1 bytes
x4F                                                                   O

7/5/14 8:56:35 PM :Debug: old style time to read outpc: 50 ms.
7/5/14 8:56:35 PM :Time: 0:07.289: Received, 52 bytes
xB0 x04 x00 x00 x30 x93 x1B x42 x90 x53 x7E x42 x00 x00 x00 x00       ....0..B.S~B....
x09 x8A x20 x3F x03 x30 x10 x41 x00 x00 x00 x00 x01 x08 x80 x3C       ...?.0.A.......<
x57 x00 x00 x00 x93 x33 x39 x42 x00 x00 xC0 x7F x01 x00 x00 x00       W....39B.......
x48 x43 x34 x42                                                       HC4B

7/5/14 8:56:35 PM :Debug: Real OchDelay for MyCar: 50, timeout=300
7/5/14 8:56:35 PM :Debug: commThreadExpectedReturnTime set to ms from now: 620
7/5/14 8:56:35 PM :Time: 0:07.305: SENT, 1 bytes
x4F                                                                   O

7/5/14 8:56:35 PM :Debug: old style time to read outpc: 49 ms.
7/5/14 8:56:35 PM :Time: 0:07.355: Received, 52 bytes
xB0 x04 x00 x00 x30 x93 x1B x42 x90 x53 x7E x42 x00 x00 x00 x00       ....0..B.S~B....
x09 x8A x20 x3F x03 x30 x10 x41 x00 x00 x00 x00 x01 x08 x80 x3C       ...?.0.A.......<
x57 x00 x00 x00 x93 x33 x39 x42 x00 x00 xC0 x7F x01 x00 x00 x00       W....39B.......
x48 x43 x34 x42                                                       HC4B

7/5/14 8:56:35 PM :Debug: Real OchDelay for MyCar: 50, timeout=300
7/5/14 8:56:35 PM :Debug: commThreadExpectedReturnTime set to ms from now: 620
7/5/14 8:56:35 PM :Time: 0:07.371: SENT, 1 bytes
x4F                                                                   O

7/5/14 8:56:35 PM :Debug: old style time to read outpc: 50 ms.
7/5/14 8:56:35 PM :Time: 0:07.421: Received, 52 bytes
xB0 x04 x00 x00 x30 x93 x1B x42 x90 x53 x7E x42 x00 x00 x00 x00       ....0..B.S~B....
x09 x8A x20 x3F x03 x30 x10 x41 x00 x00 x00 x00 x01 x08 x80 x3C       ...?.0.A.......<
x57 x00 x00 x00 x93 x33 x39 x42 x00 x00 xC0 x7F x01 x00 x00 x00       W....39B.......
x48 x43 x34 x42                                                       HC4B

7/5/14 8:56:35 PM :Debug: Real OchDelay for MyCar: 50, timeout=300
7/5/14 8:56:35 PM :Debug: commThreadExpectedReturnTime set to ms from now: 620
7/5/14 8:56:35 PM :Time: 0:07.437: SENT, 1 bytes
x4F                                                                   O

7/5/14 8:56:35 PM :Debug: old style time to read outpc: 49 ms.
7/5/14 8:56:35 PM :Time: 0:07.487: Received, 52 bytes
xB0 x04 x00 x00 x70 xC6 x1B x42 xF8 x95 x7D x42 x00 x00 x00 x00       ....p..B..}B....
x3F xEA x23 x3F x05 x54 x10 x41 x00 x00 x00 x00 x02 x0E xE0 x3C       ?.#?.T.A.......<
x5B x00 x00 x00 x36 x57 x33 x42 x00 x00 xC0 x7F x01 x00 x00 x00       [...6W3B.......
x52 x3A x34 x42                                                       R:4B

7/5/14 8:56:35 PM :Debug: Real OchDelay for MyCar: 50, timeout=300
7/5/14 8:56:35 PM :Debug: commThreadExpectedReturnTime set to ms from now: 620
7/5/14 8:56:35 PM :Time: 0:07.503: SENT, 1 bytes
x4F                                                                   O

7/5/14 8:56:35 PM :Debug: old style time to read outpc: 49 ms.
7/5/14 8:56:35 PM :Time: 0:07.553: Received, 52 bytes
xB0 x04 x00 x00 x70 xC6 x1B x42 xF8 x95 x7D x42 x00 x00 x00 x00       ....p..B..}B....
x3F xEA x23 x3F x05 x54 x10 x41 x00 x00 x00 x00 x02 x0E xE0 x3C       ?.#?.T.A.......<
x5B x00 x00 x00 x36 x57 x33 x42 x00 x00 xC0 x7F x01 x00 x00 x00       [...6W3B.......
x52 x3A x34 x42                                                       R:4B

7/5/14 8:56:35 PM :Debug: Real OchDelay for MyCar: 50, timeout=300
7/5/14 8:56:35 PM :Debug: commThreadExpectedReturnTime set to ms from now: 620
7/5/14 8:56:35 PM :Time: 0:07.569: SENT, 1 bytes
x4F                                                                   O

7/5/14 8:56:35 PM :Debug: old style time to read outpc: 49 ms.
7/5/14 8:56:35 PM :Time: 0:07.619: Received, 52 bytes
xB0 x04 x00 x00 x70 xC6 x1B x42 xF8 x95 x7D x42 x00 x00 x00 x00       ....p..B..}B....
x3F xEA x23 x3F x05 x54 x10 x41 x00 x00 x00 x00 x02 x0E xE0 x3C       ?.#?.T.A.......<
x5B x00 x00 x00 x36 x57 x33 x42 x00 x00 xC0 x7F x01 x00 x00 x00       [...6W3B.......
x52 x3A x34 x42                                                       R:4B

7/5/14 8:56:36 PM :Debug: Real OchDelay for MyCar: 50, timeout=300
7/5/14 8:56:36 PM :Debug: commThreadExpectedReturnTime set to ms from now: 620
7/5/14 8:56:36 PM :Time: 0:07.636: SENT, 1 bytes
x4F                                                                   O

7/5/14 8:56:36 PM :Debug: old style time to read outpc: 50 ms.
7/5/14 8:56:36 PM :Time: 0:07.686: Received, 52 bytes
xB0 x04 x00 x00 x70 xC6 x1B x42 xF8 x95 x7D x42 x00 x00 x00 x00       ....p..B..}B....
x3F xEA x23 x3F x05 x54 x10 x41 x00 x00 x00 x00 x02 x0E xE0 x3C       ?.#?.T.A.......<
x5B x00 x00 x00 x36 x57 x33 x42 x00 x00 xC0 x7F x01 x00 x00 x00       [...6W3B.......
x52 x3A x34 x42                                                       R:4B

7/5/14 8:56:36 PM :Debug: Real OchDelay for MyCar: 50, timeout=300
7/5/14 8:56:36 PM :Debug: commThreadExpectedReturnTime set to ms from now: 620
7/5/14 8:56:36 PM :Time: 0:07.703: SENT, 1 bytes
x4F                                                                   O

7/5/14 8:56:36 PM :Debug: old style time to read outpc: 50 ms.
7/5/14 8:56:36 PM :Time: 0:07.753: Received, 52 bytes
xB0 x04 x00 x00 x70 xC6 x1B x42 xF8 x95 x7D x42 x00 x00 x00 x00       ....p..B..}B....
x3F xEA x23 x3F x05 x54 x10 x41 x00 x00 x00 x00 x02 x0E xE0 x3C       ?.#?.T.A.......<
x5B x00 x00 x00 x36 x57 x33 x42 x00 x00 xC0 x7F x01 x00 x00 x00       [...6W3B.......
x52 x3A x34 x42                                                       R:4B

7/5/14 8:56:36 PM :Debug: Real OchDelay for MyCar: 50, timeout=300
7/5/14 8:56:36 PM :Debug: commThreadExpectedReturnTime set to ms from now: 620
7/5/14 8:56:36 PM :Time: 0:07.770: SENT, 1 bytes
x4F                                                                   O

7/5/14 8:56:36 PM :Debug: old style time to read outpc: 50 ms.
7/5/14 8:56:36 PM :Time: 0:07.820: Received, 52 bytes
xB0 x04 x00 x00 x78 xD5 x0E x42 x88 xB2 x7E x42 x00 x00 x00 x00       ....x..B..~B....
x0F xEA x20 x3F x06 x60 x10 x41 x00 x00 x00 x00 x01 x08 x00 x3D       ...?.`.A.......=
x5E x00 x00 x00 x8A x9D x38 x42 x00 x00 xC0 x7F x01 x00 x00 x00       ^.....8B.......
xBC xCC x2A x42                                                       ..*B

7/5/14 8:56:36 PM :Debug: Real OchDelay for MyCar: 50, timeout=300
7/5/14 8:56:36 PM :Debug: commThreadExpectedReturnTime set to ms from now: 620
7/5/14 8:56:36 PM :Time: 0:07.837: SENT, 1 bytes
x4F                                                                   O

7/5/14 8:56:36 PM :Debug: old style time to read outpc: 50 ms.
7/5/14 8:56:36 PM :Time: 0:07.887: Received, 52 bytes
xB0 x04 x00 x00 x78 xD5 x0E x42 x88 xB2 x7E x42 x00 x00 x00 x00       ....x..B..~B....
x0F xEA x20 x3F x06 x60 x10 x41 x00 x00 x00 x00 x01 x08 x00 x3D       ...?.`.A.......=
x5E x00 x00 x00 x8A x9D x38 x42 x00 x00 xC0 x7F x01 x00 x00 x00       ^.....8B.......
xBC xCC x2A x42                                                       ..*B

7/5/14 8:56:36 PM :Debug: Real OchDelay for MyCar: 50, timeout=300
7/5/14 8:56:36 PM :Debug: commThreadExpectedReturnTime set to ms from now: 620
7/5/14 8:56:36 PM :Time: 0:07.904: SENT, 1 bytes
x4F                                                                   O

7/5/14 8:56:36 PM :Debug: old style time to read outpc: 50 ms.
7/5/14 8:56:36 PM :Time: 0:07.954: Received, 52 bytes
xB0 x04 x00 x00 x78 xD5 x0E x42 x88 xB2 x7E x42 x00 x00 x00 x00       ....x..B..~B....
x0F xEA x20 x3F x06 x60 x10 x41 x00 x00 x00 x00 x01 x08 x00 x3D       ...?.`.A.......=
x5E x00 x00 x00 x8A x9D x38 x42 x00 x00 xC0 x7F x01 x00 x00 x00       ^.....8B.......
xBC xCC x2A x42                                                       ..*B

7/5/14 8:56:36 PM :Debug: Real OchDelay for MyCar: 50, timeout=300
7/5/14 8:56:36 PM :Debug: commThreadExpectedReturnTime set to ms from now: 620
7/5/14 8:56:36 PM :Time: 0:07.971: SENT, 1 bytes
x4F                                                                   O

7/5/14 8:56:36 PM :Debug: old style time to read outpc: 49 ms.
7/5/14 8:56:36 PM :Time: 0:08.021: Received, 52 bytes
xB0 x04 x00 x00 x78 xD5 x0E x42 x88 xB2 x7E x42 x00 x00 x00 x00       ....x..B..~B....
x0F xEA x20 x3F x06 x60 x10 x41 x00 x00 x00 x00 x01 x08 x00 x3D       ...?.`.A.......=
x5E x00 x00 x00 x8A x9D x38 x42 x00 x00 xC0 x7F x01 x00 x00 x00       ^.....8B.......
xBC xCC x2A x42                                                       ..*B

7/5/14 8:56:36 PM :Debug: Real OchDelay for MyCar: 50, timeout=300
7/5/14 8:56:36 PM :Debug: commThreadExpectedReturnTime set to ms from now: 620
7/5/14 8:56:36 PM :Time: 0:08.038: SENT, 1 bytes
x4F                                                                   O

7/5/14 8:56:36 PM :Debug: old style time to read outpc: 50 ms.
7/5/14 8:56:36 PM :Time: 0:08.088: Received, 52 bytes
xB0 x04 x00 x00 x00 x99 x18 x42 xA8 xF4 x7D x42 x00 x00 x00 x00       .......B..}B....
x3F xEA x23 x3F x05 x54 x10 x41 x00 x00 x00 x00 x02 x0E xE0 x3C       ?.#?.T.A.......<
x61 x00 x00 x00 x93 x33 x39 x42 x00 x00 xC0 x7F x01 x00 x00 x00       a....39B.......
xEA xEF x31 x42                                                       ..1B

7/5/14 8:56:36 PM :Debug: Real OchDelay for MyCar: 50, timeout=300
7/5/14 8:56:36 PM :Debug: commThreadExpectedReturnTime set to ms from now: 620
7/5/14 8:56:36 PM :Time: 0:08.104: SENT, 1 bytes
x4F                                                                   O

7/5/14 8:56:36 PM :Debug: old style time to read outpc: 49 ms.
7/5/14 8:56:36 PM :Time: 0:08.154: Received, 52 bytes
xB0 x04 x00 x00 x00 x99 x18 x42 xA8 xF4 x7D x42 x00 x00 x00 x00       .......B..}B....
x3F xEA x23 x3F x05 x54 x10 x41 x00 x00 x00 x00 x02 x0E xE0 x3C       ?.#?.T.A.......<
x61 x00 x00 x00 x93 x33 x39 x42 x00 x00 xC0 x7F x01 x00 x00 x00       a....39B.......
xEA xEF x31 x42                                                       ..1B

7/5/14 8:56:36 PM :Debug: Real OchDelay for MyCar: 50, timeout=300
7/5/14 8:56:36 PM :Debug: commThreadExpectedReturnTime set to ms from now: 620
7/5/14 8:56:36 PM :Time: 0:08.171: SENT, 1 bytes
x4F                                                                   O

7/5/14 8:56:36 PM :Debug: old style time to read outpc: 50 ms.
7/5/14 8:56:36 PM :Time: 0:08.221: Received, 52 bytes
xB0 x04 x00 x00 x00 x99 x18 x42 xA8 xF4 x7D x42 x00 x00 x00 x00       .......B..}B....
x3F xEA x23 x3F x05 x54 x10 x41 x00 x00 x00 x00 x02 x0E xE0 x3C       ?.#?.T.A.......<
x61 x00 x00 x00 x93 x33 x39 x42 x00 x00 xC0 x7F x01 x00 x00 x00       a....39B.......
xEA xEF x31 x42                                                       ..1B

7/5/14 8:56:36 PM :Debug: Real OchDelay for MyCar: 50, timeout=300
7/5/14 8:56:36 PM :Debug: commThreadExpectedReturnTime set to ms from now: 620
7/5/14 8:56:36 PM :Time: 0:08.237: SENT, 1 bytes
x4F                                                                   O

7/5/14 8:56:36 PM :Debug: old style time to read outpc: 49 ms.
7/5/14 8:56:36 PM :Time: 0:08.287: Received, 52 bytes
xB0 x04 x00 x00 x00 x99 x18 x42 xA8 xF4 x7D x42 x00 x00 x00 x00       .......B..}B....
x3F xEA x23 x3F x05 x54 x10 x41 x00 x00 x00 x00 x02 x0E xE0 x3C       ?.#?.T.A.......<
x61 x00 x00 x00 x93 x33 x39 x42 x00 x00 xC0 x7F x01 x00 x00 x00       a....39B.......
xEA xEF x31 x42                                                       ..1B
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

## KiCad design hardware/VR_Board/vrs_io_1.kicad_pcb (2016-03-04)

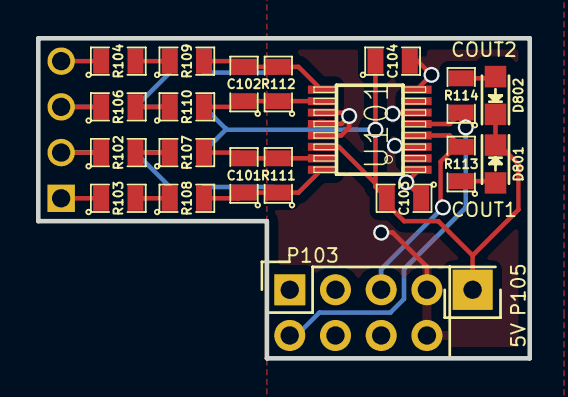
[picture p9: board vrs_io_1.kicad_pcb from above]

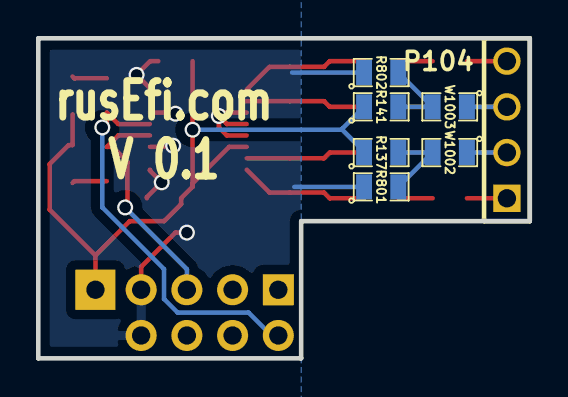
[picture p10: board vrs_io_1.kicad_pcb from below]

Board: 2 copper layers, 27.3 x 17.8 mm, 28 parts (7 on the bottom side), 20 nets.

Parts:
C101, C102: 1000pF; SM0805
C103: 10uF; SM0805
C104: 0.1uF; SM0805
D801, D802: LED-red; LED_0805
P103: CONN_02X04; Socket_Strip_Straight_2x04
P104: CONN_4; PIN_ARRAY_4x1
P105: CONN_01X01; Socket_Strip_Straight_1x01
R102, R103, R104, R106, R107, R108, R109, R110, R111, R112: 5k; SM0805
R113, R114: 10k; SM0805
R137, R141: 1K; SM0805
R801, R802: pdwn; SM0805
U101: MAX9926/9927; maxim-10-QSOP16
W1002, W1003: JMP; SM0805

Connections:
/5V: C103.2, C104.1, D801.1, D802.1, P105.1, R137.1, R141.1, U101.14
/CAM+: P104.4, R104.1
/CAM-: P104.3, R106.1, W1003.1
/CRK2+: P104.1, R103.1
/CRK2-: P104.2, R102.1, W1002.1
/Cout1: P103.5, R113.2, U101.4
/Cout2: P103.2, R114.1, U101.5
GND: C103.1, C104.2, P103.7, P103.8, R801.1, R802.1, U101.1, U101.3, U101.6, U101.8, U101.11, U101.12, U101.13
unnamed: C101.1, R108.2, R111.1, U101.16
unnamed: C101.2, R107.2, R111.2, U101.15
unnamed: C102.1, R110.2, R112.1, U101.10
unnamed: C102.2, R109.2, R112.2, U101.9
unnamed: D801.2, R113.1
unnamed: D802.2, R114.2
unnamed: R102.2, R107.1
unnamed: R103.2, R108.1
unnamed: R104.2, R109.1
unnamed: R106.2, R110.1
unnamed: R137.2, R801.2, W1002.2
unnamed: R141.2, R802.2, W1003.2

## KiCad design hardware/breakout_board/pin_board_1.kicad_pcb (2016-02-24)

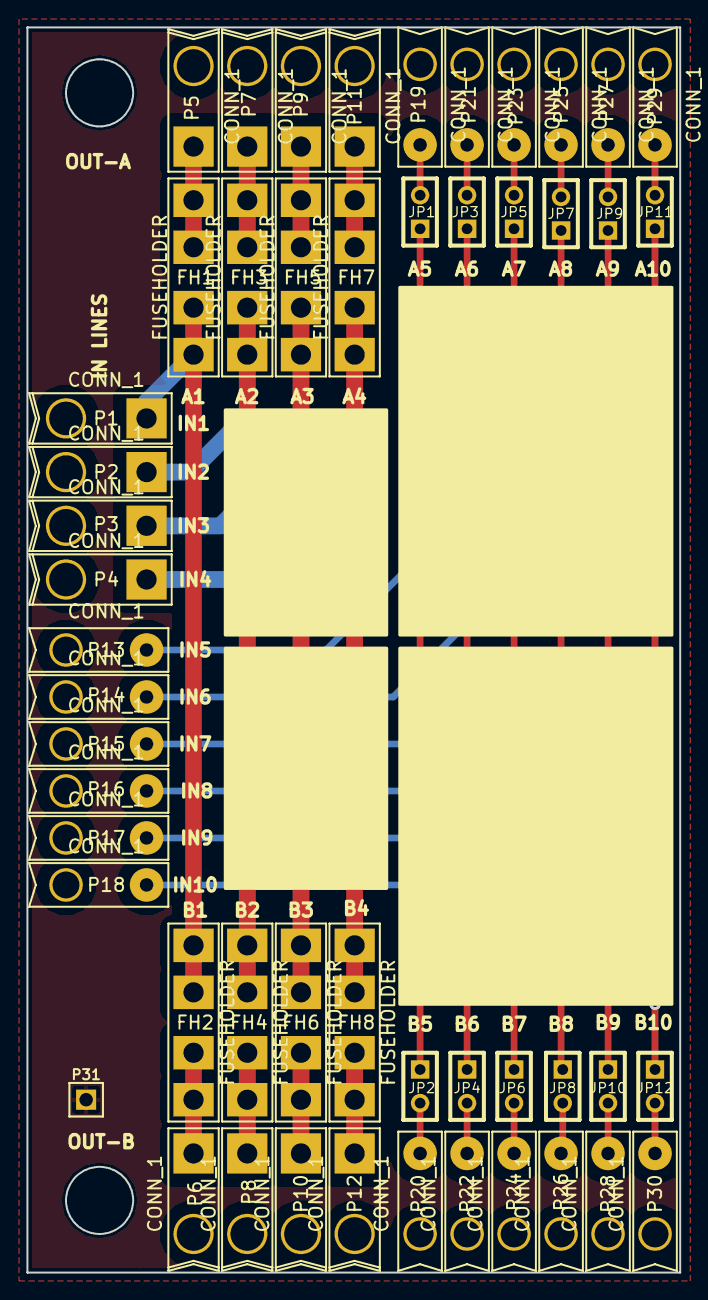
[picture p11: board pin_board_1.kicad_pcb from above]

Board: 2 copper layers, 49.4 x 94.2 mm, 51 parts (0 on the bottom side), 30 nets.

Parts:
FH1, FH2, FH3, FH4, FH5, FH6, FH7, FH8: FUSEHOLDER
JP1, JP2, JP3, JP4, JP5, JP6, JP7, JP8, JP9, JP10, JP11, JP12: JUMPER; JUMPER-2
P1, P2, P3, P4, P5, P6, P7, P8, P9, P10, P11, P12: CONN_1; PIN_1_16AWG
P13, P14, P15, P16, P17, P18, P19, P20, P21, P22, P23, P24, P25, P26, P27, P28, P29, P30: CONN_1; PIN_1_20AWG
P31: CONN_1; PIN_ARRAY_1

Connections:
unnamed: JP8.2, P26.1
unnamed: JP7.2, P25.1
unnamed: JP7.1, JP8.1, P16.1
unnamed: JP3.2, P21.1
unnamed: JP4.2, P22.1
unnamed: JP3.1, JP4.1, P14.1
unnamed: JP5.1, JP6.1, P15.1
unnamed: JP6.2, P24.1
unnamed: JP5.2, P23.1
unnamed: JP11.2, P29.1
unnamed: JP12.2, P30.1
unnamed: JP11.1, JP12.1, P18.1
unnamed: JP10.2, P28.1
unnamed: JP9.2, P27.1
unnamed: JP9.1, JP10.1, P17.1
unnamed: JP1.2, P19.1
unnamed: JP2.2, P20.1
unnamed: FH3.1, FH4.1, P2.1
unnamed: FH4.2, P8.1
unnamed: FH3.2, P7.1
unnamed: FH1.1, FH2.1, P1.1
unnamed: FH2.2, P6.1
unnamed: FH1.2, P5.1
unnamed: JP1.1, JP2.1, P13.1
unnamed: FH7.1, FH8.1, P4.1
unnamed: FH8.2, P12.1
unnamed: FH7.2, P11.1
unnamed: FH5.1, FH6.1, P3.1
unnamed: FH6.2, P10.1
unnamed: FH5.2, P9.1

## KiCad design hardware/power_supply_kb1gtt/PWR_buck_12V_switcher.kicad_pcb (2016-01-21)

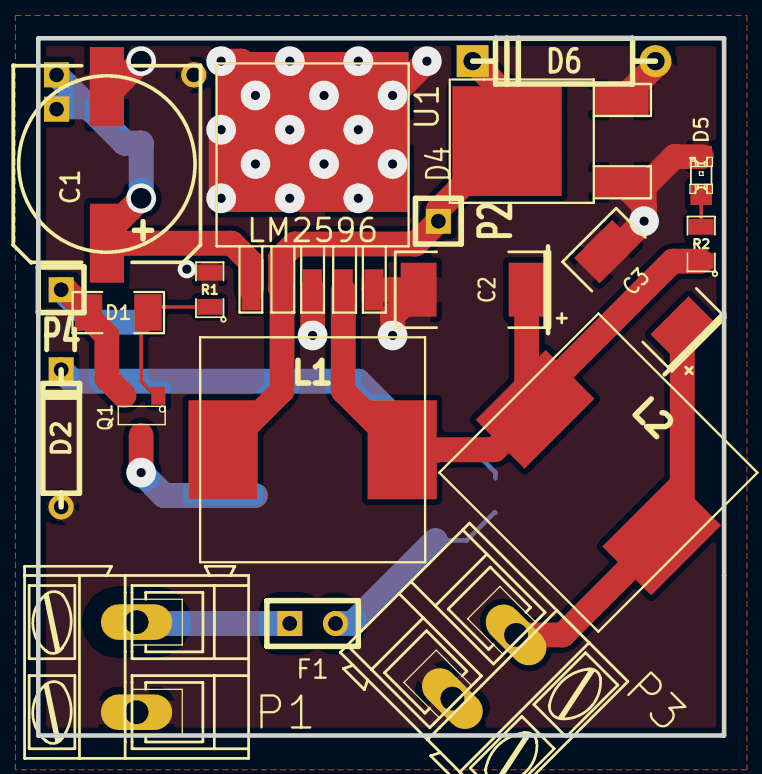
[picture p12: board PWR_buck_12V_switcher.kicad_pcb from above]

Board: 2 copper layers, 38.1 x 38.7 mm, 24 parts (0 on the bottom side), 12 nets.

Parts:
C1: 330uF 35V; SMDSVP10
C2, C3: 220uF 16V; SM2512
D1: 7.5V; SM1206
D2: 14V; D3
D3: 24V; D3
D4: SCHDPAK; DPAK2
D5: LED-grn; LED-0805
D6: DIODESCH; D4
F1: 5A; SIL-2
L1, L2, L3: 38uH; SM100uH
P1, P3: CONN_2; AK300-2
P2, P4, P5: CONN_1; SIL-1
Q1: 20V; SOT23
Q2: 200V; m-pad-2.1-TO-263AB
R1: 39k; SM0805
R2: 1k; SM0805
R3: 100k; SM0805
U1: LM2596; DPAK5

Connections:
/5V-REG: C3.1, L2.2, P3.1
/FB: C2.1, L1.2, L2.1, R2.1, U1.4
/OUT: D4.2, D6.2, L1.1, P2.1, U1.2
/VBAT: C1.1, D3.2, L3.2, P5.1, U1.1
/Vf: F1.2, Q2.3, R3.1
/Vin: F1.1, P1.2
/Vs1: D2.2, Q2.1, R3.2
/Vs2: Q1.3, Q2.2
GND: C1.2, C2.2, C3.2, D2.1, D3.1, D4.1, D4.3, D5.2, D6.1, P1.1, P3.2, R1.2, U1.3, U1.5
unnamed: D1.1, Q1.1, R1.1
unnamed: D1.2, L3.1, P4.1, Q1.2
unnamed: D5.1, R2.2

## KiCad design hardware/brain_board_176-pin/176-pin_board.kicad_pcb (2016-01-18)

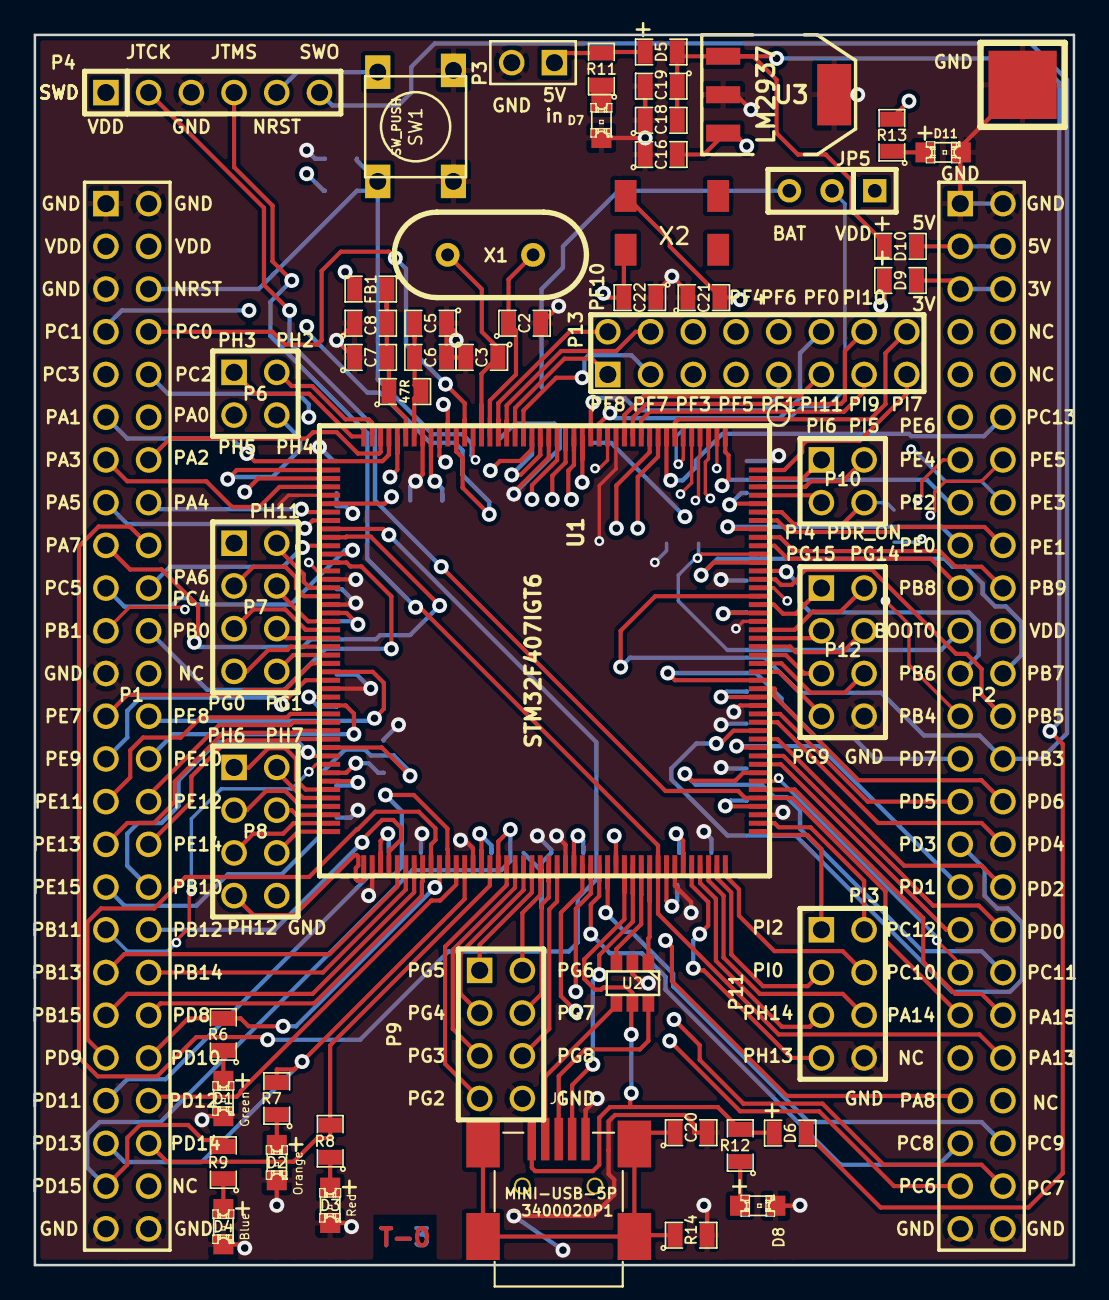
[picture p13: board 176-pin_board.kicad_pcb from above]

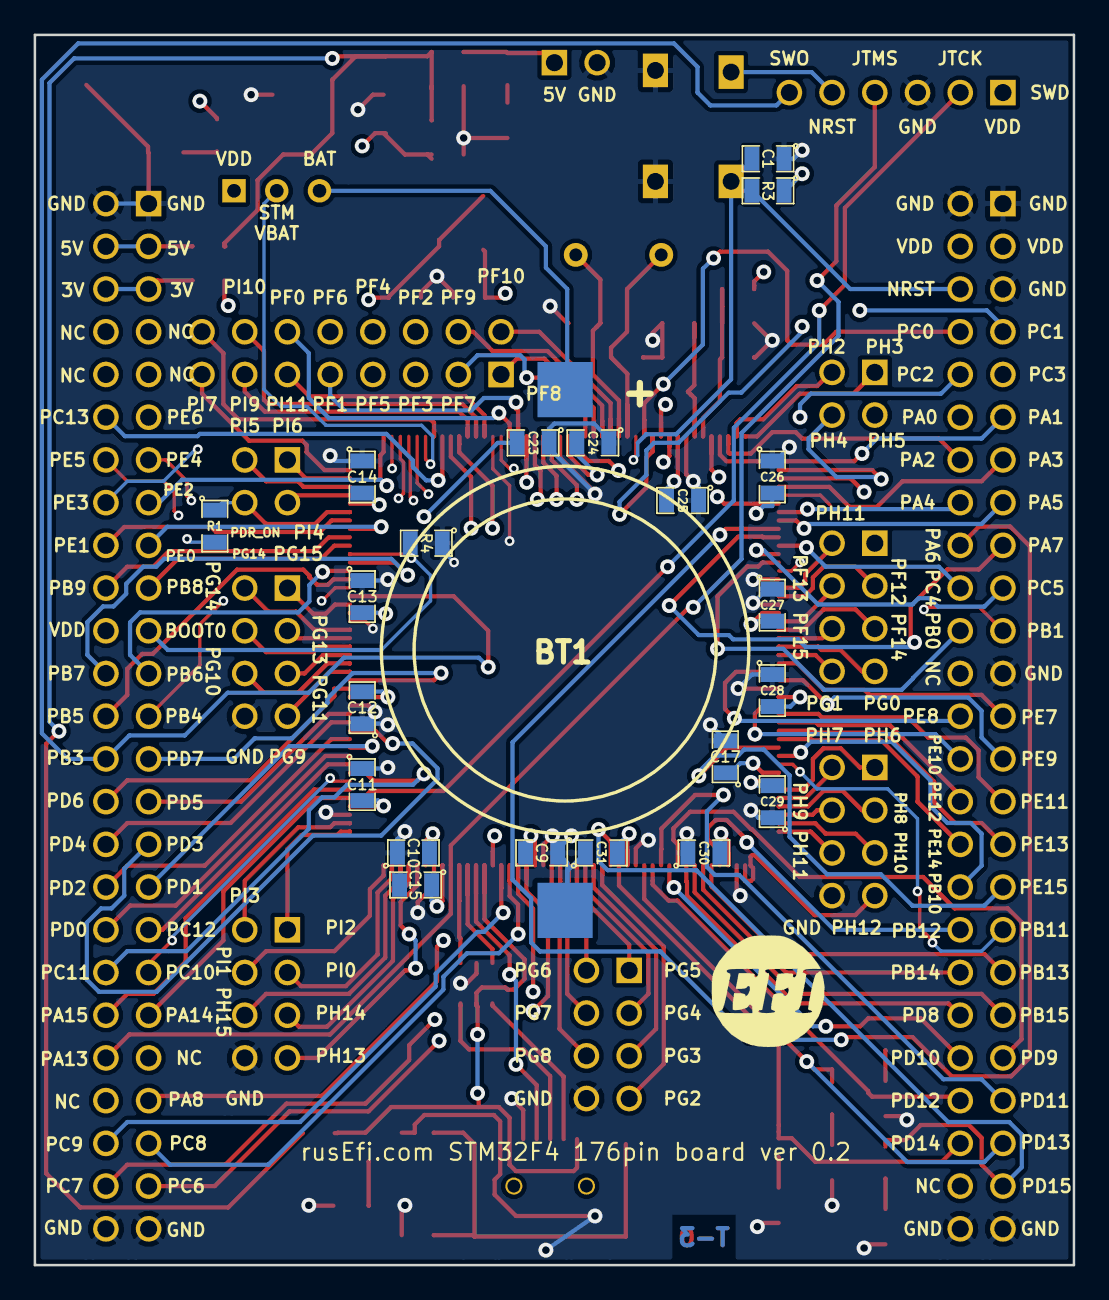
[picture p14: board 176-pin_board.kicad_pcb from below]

Board: 4 copper layers, 61.8 x 73.2 mm, 77 parts (23 on the bottom side), 164 nets.

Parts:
BT1: BATTERY_CR2032; BATT_CR2032_MPD
C1: 0.02uF; SM0805
C2, C3, C21, C22: 18pF; SM0805
C5, C8: 0.01uF; SM0805
C6, C7, C16: 1uF; SM0805
C9, C10, C11, C12, C13, C14, C18, C20, C23, C24, C25, C26, C27, C28, C29, C30, C31: 0.1uF; SM0805
C15, C17: 2u2F; SM0805
C19: 4.7uF; SM0805
D1, D2, D3, D4, D7, D8, D11: LED_0805; LED-0805_A
D5, D6, D9, D10: DIODESCH; SM0805-diode
FB1: FILTER; SM0805
G1: LOGO; LOGO_F
J1: MINI-USB-5P-3400020P1
JP5: JUMPER3; SIL-3
P1, P2: CONN_25X2; PIN_ARRAY_25x2_A
P3: CONN_2; PIN_ARRAY_2_A
P4: CONN_6; PIN_ARRAY-6X1
P5: CONN_1; 1PIN_SMD
P6, P10: CONN_2X2; PIN_ARRAY_2X2
P7, P8, P9, P11, P12: CONN_4X2; pin_array_4x2
P13: CONN_8X2; pin_array_8x2
R1, R11, R12, R13: 1k; SM0805
R3, R4: 10k; SM0805
R6, R7, R8, R9: 680R; SM0805
R10: 47R; SM0805
R14: 100k; SM0805
SW1: SW_PUSH; TL-1105
U1: STM32F407IGT6; LQFP-176
U2: NUF2101MT1G; SOT-457
U3: LM2937; SOT223
X1: CRYSTAL; HC-49V
X2: CRYSTAL(MC306); MC-306

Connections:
/3.3V: D9.2, P2.5, P2.6
/5V: D10.2, P2.3, P2.4
/5Vi: C18.2, C19.1, D5.2, D6.2, D10.1, U3.1
/BOOT0: P2.21, R4.2, U1.166
/D+: J1.3, U2.6
/D-: J1.2, U2.4
/NRST: C1.2, P1.6, P4.5, R3.2, SW1.1, U1.31
/PA0: P1.12, U1.40
/PA1: P1.11, U1.41
/PA2: P1.14, U1.42
/PA3: P1.13, U1.47
/PA4: P1.16, U1.50
/PA5: P1.15, U1.51
/PA6: P1.18, U1.52
/PA7: P1.17, U1.53
/PA8: P2.43, U1.119
/PA9: D6.1, J1.1, R12.2, U1.120, U2.5
/PA10: J1.4, U1.121
/PA11: U1.122, U2.3
/PA12: U1.123, U2.1
/PA13: P2.42, P4.4, U1.124
/PA14: P2.39, P4.2, U1.137
/PA15: P2.40, U1.138
/PB0: P1.22, U1.56
/PB1: P1.21, U1.57
/PB3: P2.28, P4.6, U1.161
/PB4: P2.25, U1.162
/PB5: P2.26, U1.163
/PB6: P2.23, U1.164
/PB7: P2.24, U1.165
/PB8: P2.19, U1.167
/PB9: P2.20, U1.168
/PB10: P1.34, U1.79
/PB11: P1.35, U1.80
/PB12: P1.36, U1.92
/PB13: P1.37, U1.93
/PB14: P1.38, U1.94
/PB15: P1.39, U1.95
/PC0: P1.8, U1.32
/PC1: P1.7, U1.33
/PC2: P1.10, U1.34
/PC3: P1.9, U1.35
/PC4: P1.20, U1.54
/PC5: P1.19, U1.55
/PC6: P2.47, U1.115
/PC7: P2.48, U1.116
/PC8: P2.45, U1.117
/PC9: P2.46, U1.118
/PC10: P2.37, U1.139
/PC11: P2.38, U1.140
/PC12: P2.35, U1.141
/PC13: P2.12, U1.8
/PD0: P2.36, U1.142
/PD1: P2.33, U1.143
/PD2: P2.34, U1.144
/PD3: P2.31, U1.145
/PD4: P2.32, U1.146
/PD5: P2.29, U1.147
/PD6: P2.30, U1.150
/PD7: P2.27, U1.151
/PD8: P1.40, U1.96
/PD9: P1.41, U1.97
/PD10: P1.42, R6.2, U1.98
/PD11: P1.43, U1.99
/PD12: P1.44, U1.100
/PD13: P1.45, R7.2, U1.101
/PD14: P1.46, R8.2, U1.104
/PD15: P1.47, R9.2, U1.105
/PDR_ON: P10.4, R1.1, U1.171
/PE0: P2.17, U1.169
/PE1: P2.18, U1.170
/PE2: P2.15, U1.1
/PE3: P2.16, U1.2
/PE4: P2.13, U1.3
/PE5: P2.14, U1.4
/PE6: P2.11, U1.5
/PE7: P1.25, U1.68
/PE8: P1.26, U1.69
/PE9: P1.27, U1.70
/PE10: P1.28, U1.73
/PE11: P1.29, U1.74
/PE12: P1.30, U1.75
/PE13: P1.31, U1.76
/PE14: P1.32, U1.77
/PE15: P1.33, U1.78
/PF0: P13.12, U1.16
/PF1: P13.9, U1.17
/PF2: P13.6, U1.18
/PF3: P13.5, U1.19
/PF4: P13.8, U1.20
/PF5: P13.7, U1.21
/PF6: P13.10, U1.24
/PF7: P13.3, U1.25
/PF8: P13.1, U1.26
/PF9: P13.4, U1.27
/PF10: P13.2, U1.28
/PF11: P7.2, U1.59
/PF12: P7.3, U1.60
/PF13: P7.4, U1.63
/PF14: P7.5, U1.64
/PF15: P7.6, U1.65
/PG0: P7.7, U1.66
/PG1: P7.8, U1.67
/PG2: P9.7, U1.106
/PG3: P9.5, U1.107
/PG4: P9.3, U1.108
/PG5: P9.1, U1.109
/PG6: P9.2, U1.110
/PG7: P9.4, U1.111
/PG8: P9.6, U1.112
/PG9: P12.7, U1.152
/PG10: P12.6, U1.153
/PG11: P12.5, U1.154
/PG12: P12.4, U1.155
/PG13: P12.3, U1.156
/PG14: P12.2, U1.157
/PG15: P12.1, U1.160
/PH0: C2.1, U1.29, X1.2
/PH1: C3.1, U1.30, X1.1
/PH2: P6.2, U1.43
/PH3: P6.1, U1.44
/PH4: P6.4, U1.45
/PH5: P6.3, U1.46
/PH6: P8.1, U1.83
/PH7: P8.2, U1.84
/PH8: P8.3, U1.85
/PH9: P8.4, U1.86
/PH10: P8.5, U1.87
/PH11: P8.6, U1.88
/PH12: P8.7, U1.89
/PH13: P11.7, U1.128
/PH14: P11.5, U1.129
/PH15: P11.6, U1.130
/PI0: P11.3, U1.131
/PI1: P11.4, U1.132
/PI2: P11.1, U1.133
/PI3: P11.2, U1.134
/PI4: P10.3, U1.173
/PI5: P10.2, U1.174
/PI6: P10.1, U1.175
/PI7: P13.15, U1.176
/PI8: P13.16, U1.7
/PI9: P13.13, U1.11
/PI10: P13.14, U1.12
/PI11: P13.11, U1.13
/VBAT: JP5.2, U1.6
/VDD: C9.2, C10.2, C11.2, C12.2, C13.2, C14.2, C16.2, C23.2, C24.2, C25.2, C26.2, C27.2, C28.2, C29.2, C30.2, C31.2, D9.1, FB1.2, JP5.1, P1.3, P1.4, P2.22, P4.1, R1.2, R3.1, R13.2, U1.15, U1.23, U1.36, U1.49, U1.62, U1.72, U1.82, U1.91, U1.103, U1.114, U1.127, U1.136, U1.149, U1.159, U1.172, U3.3
GND: BT1.2, C1.1, C2.2, C3.2, C5.1, C6.1, C7.1, C8.1, C9.1, C10.1, C11.1, C12.1, C13.1, C14.1, C15.2, C16.1, C17.2, C18.1, C19.2, C20.2, C21.1, C22.1, C23.1, C24.1, C25.1, C26.1, C27.1, C28.1, C29.1, C30.1, C31.1, D1.2, D2.2, D3.2, D4.2, D7.2, D8.2, D11.2, J1.5, P1.1, P1.2, P1.5, P1.23, P1.49, P1.50, P2.1, P2.2, P2.49, P2.50, P3.2, P4.3, P5.1, P8.8, P9.8, P11.8, P12.8, R4.1, R14.2, SW1.2, U1.14, U1.22, U1.37, U1.48, U1.58, U1.61, U1.71, U1.90, U1.102, U1.113, U1.126, U1.135, U1.148, U1.158, U2.2, U3.2, U3.4
unnamed: C7.2, C8.2, FB1.1, R10.1, U1.39
unnamed: D11.1, R13.1
unnamed: D2.1, R7.1
unnamed: D1.1, R6.1
unnamed: C5.2, C6.2, R10.2, U1.38
unnamed: D3.1, R8.1
unnamed: D5.1, P3.1, R11.2
unnamed: BT1.1, JP5.3
unnamed: D4.1, R9.1
unnamed: D7.1, R11.1
unnamed: D8.1, R12.1
unnamed: C20.1, J1.6, R14.1
unnamed: C21.2, U1.9, X2.4
unnamed: C22.2, U1.10, X2.1
unnamed: C15.1, U1.125
unnamed: C17.1, U1.81

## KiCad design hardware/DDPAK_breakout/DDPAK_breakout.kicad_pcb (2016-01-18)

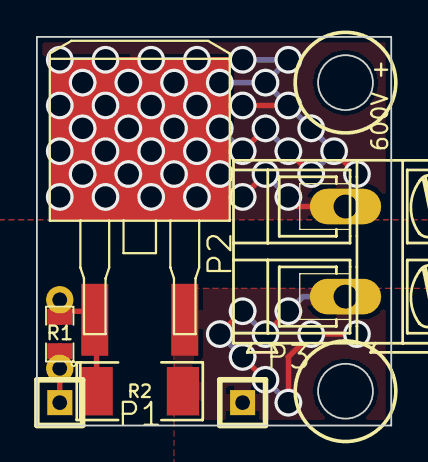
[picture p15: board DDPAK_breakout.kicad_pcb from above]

Board: 2 copper layers, 19.7 x 21.6 mm, 6 parts (0 on the bottom side), 4 nets.

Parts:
P1, P3: CONN_1; SIL-1
P2: CONN_2; AK300-2
Q1: IRGS14C40L; m-pad-2.1-TO-263AB
R1: 1K; SM0805_jumper
R2: 100K; SM2010

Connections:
/GND: P2.2, P3.1, Q1.3, R2.2
/HV: P2.1, Q1.2
/SIG: P1.1, R1.1
/SIG2: Q1.1, R1.2, R2.1

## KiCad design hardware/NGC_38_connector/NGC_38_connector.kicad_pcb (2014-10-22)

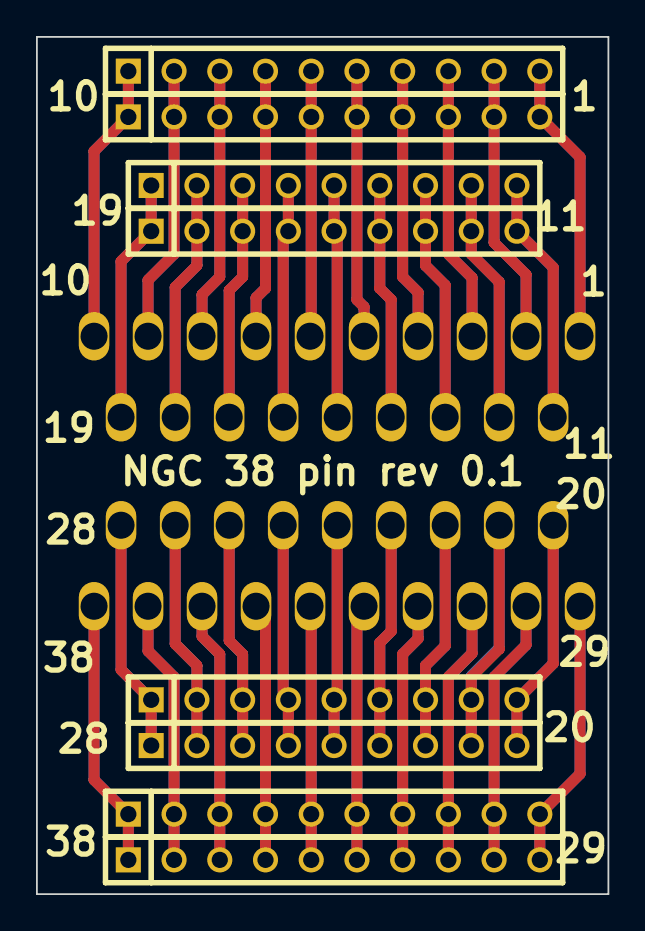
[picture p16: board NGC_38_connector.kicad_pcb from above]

Board: 2 copper layers, 31.8 x 47.6 mm, 9 parts (0 on the bottom side), 38 nets.

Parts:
P1: DIL38; PCM_C1
P2, P4, P6, P9: CONN_10; SIL-10
P3, P5, P7, P8: CONN_9; SIL-9

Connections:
unnamed: P1.1, P2.1, P6.1
unnamed: P1.2, P2.2, P6.2
unnamed: P1.3, P2.3, P6.3
unnamed: P1.4, P2.4, P6.4
unnamed: P1.5, P2.5, P6.5
unnamed: P1.6, P2.6, P6.6
unnamed: P1.7, P2.7, P6.7
unnamed: P1.8, P2.8, P6.8
unnamed: P1.9, P2.9, P6.9
unnamed: P1.10, P2.10, P6.10
unnamed: P1.17, P3.7, P7.7
unnamed: P1.24, P5.5, P8.5
unnamed: P1.25, P5.6, P8.6
unnamed: P1.26, P5.7, P8.7
unnamed: P1.27, P5.8, P8.8
unnamed: P1.28, P5.9, P8.9
unnamed: P1.11, P3.1, P7.1
unnamed: P1.12, P3.2, P7.2
unnamed: P1.13, P3.3, P7.3
unnamed: P1.14, P3.4, P7.4
unnamed: P1.15, P3.5, P7.5
unnamed: P1.16, P3.6, P7.6
unnamed: P1.23, P5.4, P8.4
unnamed: P1.18, P3.8, P7.8
unnamed: P1.19, P3.9, P7.9
unnamed: P1.31, P4.3, P9.3
unnamed: P1.29, P4.1, P9.1
unnamed: P1.30, P4.2, P9.2
unnamed: P1.32, P4.4, P9.4
unnamed: P1.33, P4.5, P9.5
unnamed: P1.34, P4.6, P9.6
unnamed: P1.35, P4.7, P9.7
unnamed: P1.36, P4.8, P9.8
unnamed: P1.37, P4.9, P9.9
unnamed: P1.38, P4.10, P9.10
unnamed: P1.20, P5.1, P8.1
unnamed: P1.21, P5.2, P8.2
unnamed: P1.22, P5.3, P8.3

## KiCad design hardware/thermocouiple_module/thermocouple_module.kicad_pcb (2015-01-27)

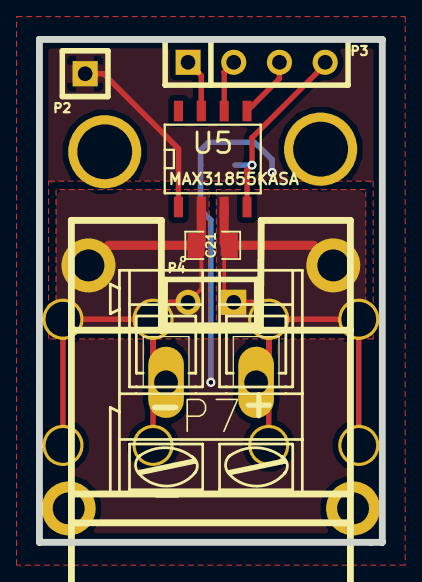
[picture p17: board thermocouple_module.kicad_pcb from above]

Board: 2 copper layers, 19.0 x 27.9 mm, 12 parts (1 on the bottom side), 7 nets.

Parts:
C8: 100nF; SM0805-SM0603
C21: 10nF; SM0805-SM0603
P1: CONN_2; tcpl_PCC-SMP
P2: CONN_1; SIL-1
P3: CONN_4; SIL-4
P4: CONN_2; SIL-2
P5, P6: CONN_1; SCREW_TERM_534-7693
P7: CONN_2; AK300-2
U5: MAX31855KASA; SO8E
V801, V802: VIA; 1pin

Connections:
3.3v: C8.1, P3.4, U5.4
//CS: P3.2, U5.6
/MISO: P3.1, U5.7
/SCK: P3.3, U5.5
/TCPL+: C21.2, P1.2, P4.1, P6.1, P7.1, U5.3
/TCPL-: C21.1, P1.1, P4.2, P5.1, P7.2, U5.2
GND: C8.2, P2.1, U5.1

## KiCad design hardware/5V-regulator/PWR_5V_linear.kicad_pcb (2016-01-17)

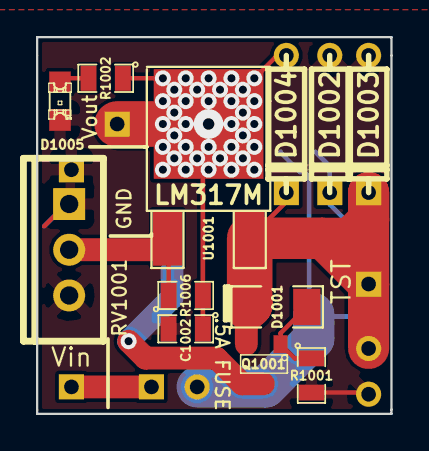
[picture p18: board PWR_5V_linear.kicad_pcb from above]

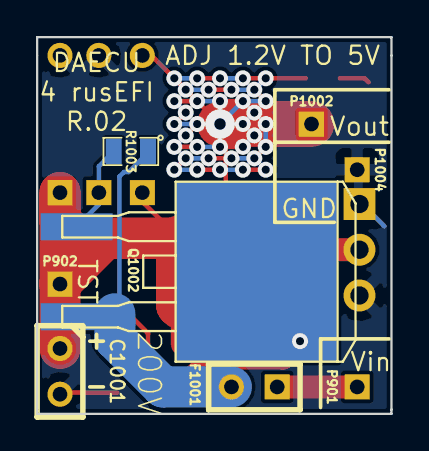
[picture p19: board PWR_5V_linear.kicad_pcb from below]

Board: 2 copper layers, 19.7 x 20.9 mm, 20 parts (8 on the bottom side), 10 nets.

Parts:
C1001: 0.1uF 50V; C1
C1002: 1uF 16V; SM0805
D1001: 7.5V; SM1206
D1002: 15V; D3
D1003, D1004: 24V; D3
D1005: LED-grn; LED-0805
F1001: 5A; SIL-2
P901, P902, P1002, P1004: CONN_1; SIL-1
Q1001: 30V; SOT23
Q1002: 200V; m-pad-2.1-TO-263AB
R1001, R1002: 1k; SM0805
R1003: 100k; SM0805
R1006: 240R; SM0805
RV1001: 1k; TO220_VERT
U1001: LM317M; DPAK2

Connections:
/5V-REG: C1002.1, D1004.1, P1002.1, R1002.1, R1006.2, U1001.2
/VBAT: C1001.1, D1001.2, D1003.2, D1004.2, P902.1, Q1001.2, U1001.3
/Vf: F1001.2, Q1002.3, R1003.1
/Vin: F1001.1, P901.1
/Vs1: D1002.2, Q1002.1, R1003.2
/Vs2: Q1001.3, Q1002.2
GND: C1001.2, C1002.2, D1002.1, D1003.1, D1005.2, P1004.1, R1001.2, RV1001.1, RV1001.2
unnamed: R1006.1, RV1001.3, U1001.1
unnamed: D1001.1, Q1001.1, R1001.1
unnamed: D1005.1, R1002.2

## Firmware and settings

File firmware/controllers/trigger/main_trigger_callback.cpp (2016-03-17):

/**
 * @file    main_trigger_callback.cpp
 * @brief   Main logic is here!
 *
 * See http://rusefi.com/docs/html/
 *
 * @date Feb 7, 2013
 * @author Andrey Belomutskiy, (c) 2012-2016
 *
 * This file is part of rusEfi - see http://rusefi.com
 *
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
 * You should have received a copy of the GNU General Public License along with this program.
 * If not, see <http://www.gnu.org/licenses/>.
 */

#include "main.h"
#if EFI_PROD_CODE || defined(__DOXYGEN__)
#include <nvic.h>
#endif

#if (!EFI_PROD_CODE && !EFI_SIMULATOR) || defined(__DOXYGEN__)

#define chThdSelf() 0
#define getRemainingStack(x) (999999)

#endif

#if EFI_ENGINE_CONTROL || defined(__DOXYGEN__)

#include "main_trigger_callback.h"
#include "efiGpio.h"
#include "engine_math.h"
#include "trigger_central.h"
#include "rpm_calculator.h"
#include "signal_executor.h"
#include "engine_configuration.h"
#include "interpolation.h"
#include "advance_map.h"
#include "allsensors.h"
#include "cyclic_buffer.h"
#include "histogram.h"
#include "fuel_math.h"
#include "histogram.h"
#if EFI_PROD_CODE || defined(__DOXYGEN__)
#include "rfiutil.h"
#endif /* EFI_HISTOGRAMS */
#include "LocalVersionHolder.h"
#include "event_queue.h"
#include "engine.h"
#include "efilib2.h"

EXTERN_ENGINE
;
extern bool hasFirmwareErrorFlag;

static LocalVersionHolder triggerVersion;

extern engine_pins_s enginePins;
static MainTriggerCallback mainTriggerCallbackInstance;

/**
 * In order to archive higher event precision, we are using a hybrid approach
 * where we are scheduling events based on the closest trigger event with a time offset.
 *
 * This queue is using global trigger event index as 'time'
 */
//static EventQueue triggerEventsQueue;
static cyclic_buffer<int> ignitionErrorDetection;

static Logging *logger;

// todo: figure out if this even helps?
//#if defined __GNUC__
//#define RAM_METHOD_PREFIX __attribute__((section(".ram")))
//#else
//#define RAM_METHOD_PREFIX
//#endif

static void startSimultaniousInjection(Engine *engine) {
	for (int i = 0; i < engine->engineConfiguration->specs.cylindersCount; i++) {
		turnPinHigh(&enginePins.injectors[i]);
	}
}

static void endSimultaniousInjection(Engine *engine) {
	for (int i = 0; i < engine->engineConfiguration->specs.cylindersCount; i++) {
		turnPinLow(&enginePins.injectors[i]);
	}
}

static ALWAYS_INLINE void handleFuelInjectionEvent(int eventIndex, bool limitedFuel, InjectionEvent *event,
		int rpm DECLARE_ENGINE_PARAMETER_S) {
	if (limitedFuel)
		return; // todo: move this check up

	/**
	 * todo: this is a bit tricky with batched injection. is it? Does the same
	 * wetting coefficient works the same way for any injection mode, or is something
	 * x2 or /2?
	 */
	floatms_t injectionDuration = ENGINE(wallFuel).adjust(event->injectorIndex, ENGINE(fuelMs) PASS_ENGINE_PARAMETER);

	ENGINE(actualLastInjection) = injectionDuration;
	if (cisnan(injectionDuration)) {
		warning(OBD_PCM_Processor_Fault, "NaN injection pulse");
		return;
	}
	if (injectionDuration < 0) {
		warning(OBD_PCM_Processor_Fault, "Negative injection pulse %f", injectionDuration);
		return;
	}

	if (engine->isCylinderCleanupMode)
		return;

	floatus_t injectionStartDelayUs = ENGINE(rpmCalculator.oneDegreeUs) * event->injectionStart.angleOffset;

	OutputSignal *signal = &ENGINE(engineConfiguration2)->fuelActuators[eventIndex];

	if (event->isSimultanious) {
		if (injectionDuration < 0) {
			firmwareError("duration cannot be negative: %d", injectionDuration);
			return;
		}
		if (cisnan(injectionDuration)) {
			firmwareError("NaN in scheduleOutput", injectionDuration);
			return;
		}
		/**
		 * this is pretty much copy-paste of 'scheduleOutput'
		 * 'scheduleOutput' is currently only used for injection, so maybe it should be
		 * changed into 'scheduleInjection' and unified? todo: think about it.
		 */
		efiAssertVoid(signal!=NULL, "signal is NULL");
		int index = getRevolutionCounter() % 2;
		scheduling_s * sUp = &signal->signalTimerUp[index];
		scheduling_s * sDown = &signal->signalTimerDown[index];

		scheduleTask("out up", sUp, (int) injectionStartDelayUs, (schfunc_t) &startSimultaniousInjection, engine);
		scheduleTask("out down", sDown, (int) injectionStartDelayUs + MS2US(injectionDuration),
					(schfunc_t) &endSimultaniousInjection, engine);

	} else {
#if EFI_UNIT_TEST || defined(__DOXYGEN__)
		printf("scheduling injection angle=%f/delay=%f injectionDuration=%f\r\n", event->injectionStart.angleOffset, injectionStartDelayUs, injectionDuration);
#endif

		scheduleOutput(signal, getTimeNowUs(), injectionStartDelayUs, MS2US(injectionDuration), event->output);
	}
}

static ALWAYS_INLINE void handleFuel(bool limitedFuel, uint32_t eventIndex, int rpm DECLARE_ENGINE_PARAMETER_S) {
	if (!isInjectionEnabled(engineConfiguration))
		return;
	efiAssertVoid(getRemainingStack(chThdSelf()) > 128, "lowstck#3");
	efiAssertVoid(eventIndex < ENGINE(triggerShape.getLength()), "handleFuel/event index");

	/**
	 * Ignition events are defined by addFuelEvents() according to selected
	 * fueling strategy
	 */
	FuelSchedule *fs = ENGINE(engineConfiguration2)->injectionEvents;

	InjectionEventList *source = &fs->injectionEvents;

	if (!fs->hasEvents[eventIndex])
		return;

	ENGINE(tpsAccelEnrichment.onNewValue(getTPS(PASS_ENGINE_PARAMETER_F) PASS_ENGINE_PARAMETER));
	ENGINE(engineLoadAccelEnrichment.onEngineCycle(PASS_ENGINE_PARAMETER_F));

	ENGINE(fuelMs) = getFuelMs(rpm PASS_ENGINE_PARAMETER) * CONFIG(globalFuelCorrection);

	for (int i = 0; i < source->size; i++) {
		InjectionEvent *event = &source->elements[i];
		if (event->injectionStart.eventIndex != eventIndex)
			continue;
		handleFuelInjectionEvent(i, limitedFuel, event, rpm PASS_ENGINE_PARAMETER);
	}
}

static ALWAYS_INLINE void handleSparkEvent(bool limitedSpark, uint32_t eventIndex, IgnitionEvent *iEvent,
		int rpm DECLARE_ENGINE_PARAMETER_S) {

	float dwellMs = ENGINE(engineState.sparkDwell);
	if (cisnan(dwellMs) || dwellMs < 0) {
		firmwareError("invalid dwell: %f at %d", dwellMs, rpm);
		return;
	}

	floatus_t chargeDelayUs = ENGINE(rpmCalculator.oneDegreeUs) * iEvent->dwellPosition.angleOffset;
	int isIgnitionError = chargeDelayUs < 0;
	ignitionErrorDetection.add(isIgnitionError);
	if (isIgnitionError) {
#if EFI_PROD_CODE || defined(__DOXYGEN__)
		scheduleMsg(logger, "Negative spark delay=%f", chargeDelayUs);
#endif
		chargeDelayUs = 0;
		return;
	}

	if (cisnan(dwellMs)) {
		firmwareError("NaN in scheduleOutput", dwellMs);
		return;
	}

	/**
	 * We are alternating two event lists in order to avoid a potential issue around revolution boundary
	 * when an event is scheduled within the next revolution.
	 */
	scheduling_s * sUp = &iEvent->signalTimerUp;
	scheduling_s * sDown = &iEvent->signalTimerDown;

	/**
	 * The start of charge is always within the current trigger event range, so just plain time-based scheduling
	 */
	if (!limitedSpark) {
#if EFI_UNIT_TEST || defined(__DOXYGEN__)
	printf("spark charge delay=%f\r\n", chargeDelayUs);
#endif
		/**
		 * Note how we do not check if spark is limited or not while scheduling 'spark down'
		 * This way we make sure that coil dwell started while spark was enabled would fire and not burn
		 * the coil.
		 */
		scheduleTask("spark up", sUp, chargeDelayUs, (schfunc_t) &turnPinHigh, iEvent->output);
	}
	/**
	 * Spark event is often happening during a later trigger event timeframe
	 * TODO: improve precision
	 */

	findTriggerPosition(&iEvent->sparkPosition, iEvent->advance PASS_ENGINE_PARAMETER);

	if (iEvent->sparkPosition.eventIndex == eventIndex) {
		/**
		 * Spark should be fired before the next trigger event - time-based delay is best precision possible
		 */
		float timeTillIgnitionUs = ENGINE(rpmCalculator.oneDegreeUs) * iEvent->sparkPosition.angleOffset;

#if EFI_UNIT_TEST || defined(__DOXYGEN__)
	printf("spark delay=%f angle=%f\r\n", timeTillIgnitionUs, iEvent->sparkPosition.angleOffset);
#endif

	scheduleTask("spark1 down", sDown, (int) timeTillIgnitionUs, (schfunc_t) &turnPinLow, iEvent->output);
	} else {
		/**
		 * Spark should be scheduled in relation to some future trigger event, this way we get better firing precision
		 */
		bool isPending = assertNotInList<IgnitionEvent>(ENGINE(iHead), iEvent);
		if (isPending)
			return;

		LL_APPEND(ENGINE(iHead), iEvent);
	}
}

static ALWAYS_INLINE void handleSpark(bool limitedSpark, uint32_t eventIndex, int rpm,
		IgnitionEventList *list DECLARE_ENGINE_PARAMETER_S) {
	if (!isValidRpm(rpm) || !CONFIG(isIgnitionEnabled))
		return; // this might happen for instance in case of a single trigger event after a pause

	/**
	 * Ignition schedule is defined once per revolution
	 * See initializeIgnitionActions()
	 */

	IgnitionEvent *current, *tmp;

	LL_FOREACH_SAFE(ENGINE(iHead), current, tmp)
	{
		if (current->sparkPosition.eventIndex == eventIndex) {
			// time to fire a spark which was scheduled previously
			LL_DELETE(ENGINE(iHead), current);

			scheduling_s * sDown = &current->signalTimerDown;

			float timeTillIgnitionUs = ENGINE(rpmCalculator.oneDegreeUs) * current->sparkPosition.angleOffset;
			scheduleTask("spark 2down", sDown, (int) timeTillIgnitionUs, (schfunc_t) &turnPinLow, current->output);
		}
	}

//	scheduleSimpleMsg(&logger, "eventId spark ", eventIndex);
	for (int i = 0; i < list->size; i++) {
		IgnitionEvent *event = &list->elements[i];
		if (event->dwellPosition.eventIndex != eventIndex)
			continue;
		handleSparkEvent(limitedSpark, eventIndex, event, rpm PASS_ENGINE_PARAMETER);
	}
}

static histogram_s mainLoopHisto;

void showMainHistogram(void) {
#if EFI_PROD_CODE || defined(__DOXYGEN__)
	printHistogram(logger, &mainLoopHisto);
#endif
}

// todo: the method name is not correct any more - no calc is done here anymore
static ALWAYS_INLINE void ignitionMathCalc(int rpm DECLARE_ENGINE_PARAMETER_S) {
	/**
	 * Within one engine cycle all cylinders are fired with same timing advance.
	 * todo: one day we can control cylinders individually?
	 */
	float dwellMs = ENGINE(engineState.sparkDwell);

	if (cisnan(dwellMs) || dwellMs < 0) {
		firmwareError("invalid dwell: %f at %d", dwellMs, rpm);
		return;
	}
}

#if EFI_PROD_CODE || defined(__DOXYGEN__)
/**
 * this field is used as an Expression in IAR debugger
 */
uint32_t *cyccnt = (uint32_t*) &DWT->CYCCNT;
#endif

static ALWAYS_INLINE void scheduleIgnitionAndFuelEvents(int rpm, int revolutionIndex DECLARE_ENGINE_PARAMETER_S) {

	engine->m.beforeIgnitionSch = GET_TIMESTAMP();
	/**
	 * TODO: warning. there is a bit of a hack here, todo: improve.
	 * currently output signals/times signalTimerUp from the previous revolutions could be
	 * still used because they have crossed the revolution boundary
	 * but we are already re-purposing the output signals, but everything works because we
	 * are not affecting that space in memory. todo: use two instances of 'ignitionSignals'
	 */
	float maxAllowedDwellAngle = (int) (getEngineCycle(engineConfiguration->operationMode) / 2); // the cast is about making Coverity happy

	if (engineConfiguration->ignitionMode == IM_ONE_COIL) {
		maxAllowedDwellAngle = getEngineCycle(engineConfiguration->operationMode) / engineConfiguration->specs.cylindersCount / 1.1;
	}

	if (engine->engineState.dwellAngle == 0) {
		warning(OBD_PCM_Processor_Fault, "dwell is zero?");
	}
	if (engine->engineState.dwellAngle > maxAllowedDwellAngle) {
		warning(OBD_PCM_Processor_Fault, "dwell angle too long: %f", engine->engineState.dwellAngle);
	}

	// todo: add some check for dwell overflow? like 4 times 6 ms while engine cycle is less then that

	IgnitionEventList *list = &engine->engineConfiguration2->ignitionEvents[revolutionIndex];

	if (cisnan(ENGINE(engineState.timingAdvance))) {
		// error should already be reported
		list->reset(); // reset is needed to clear previous ignition schedule
		return;
	}
	initializeIgnitionActions(ENGINE(engineState.timingAdvance), ENGINE(engineState.dwellAngle), list PASS_ENGINE_PARAMETER);
	engine->m.ignitionSchTime = GET_TIMESTAMP() - engine->m.beforeIgnitionSch;

//	engine->prepareFuelSchedule(PASS_ENGINE_PARAMETER_F);
}

/**
 * This is the main trigger event handler.
 * Both injection and ignition are controlled from this method.
 */
void mainTriggerCallback(trigger_event_e ckpSignalType, uint32_t eventIndex DECLARE_ENGINE_PARAMETER_S) {
	ENGINE(m.beforeMainTrigger) = GET_TIMESTAMP();
	if (hasFirmwareError()) {
		/**
		 * In case on a major error we should not process any more events.
		 * TODO: add 'pin shutdown' invocation somewhere - coils might be still open here!
		 */
		return;
	}

	(void) ckpSignalType;
	efiAssertVoid(eventIndex < 2 * engine->triggerShape.getSize(), "trigger/event index");
	efiAssertVoid(getRemainingStack(chThdSelf()) > 128, "lowstck#2");

	int rpm = ENGINE(rpmCalculator.rpmValue);
	if (rpm == 0) {
		// this happens while we just start cranking
		// todo: check for 'trigger->is_synchnonized?'
		// TODO: add 'pin shutdown' invocation somewhere - coils might be still open here!
		return;
	}
	if (rpm == NOISY_RPM) {
		warning(OBD_Camshaft_Position_Sensor_Circuit_Range_Performance, "noisy trigger");
		// TODO: add 'pin shutdown' invocation somewhere - coils might be still open here!
		return;
	}
	bool limitedSpark = rpm > CONFIG(rpmHardLimit);
	bool limitedFuel = rpm > CONFIG(rpmHardLimit);

	if (CONFIG(boostCutPressure) !=0) {
		if (getMap() > CONFIG(boostCutPressure)) {
			limitedSpark = true;
			limitedFuel = true;
		}
	}

	if (limitedSpark || limitedFuel) {
		warning(OBD_PCM_Processor_Fault, "skipping stroke due to rpm=%d", rpm);
	}

#if (EFI_HISTOGRAMS && EFI_PROD_CODE) || defined(__DOXYGEN__)
	int beforeCallback = hal_lld_get_counter_value();
#endif

	int revolutionIndex = ENGINE(rpmCalculator).getRevolutionCounter() % 2;

	if (eventIndex == 0) {
		if (triggerVersion.isOld())
			prepareOutputSignals(PASS_ENGINE_PARAMETER_F);
	}

	efiAssertVoid(!CONFIG(useOnlyRisingEdgeForTrigger) || CONFIG(ignMathCalculateAtIndex) % 2 == 0, "invalid ignMathCalculateAtIndex");

	if (eventIndex == CONFIG(ignMathCalculateAtIndex)) {
		if (CONFIG(externalKnockSenseAdc) != EFI_ADC_NONE) {
			float externalKnockValue = getVoltageDivided("knock", engineConfiguration->externalKnockSenseAdc);
			engine->knockLogic(externalKnockValue);
		}

		ENGINE(m.beforeIgnitionMath) = GET_TIMESTAMP();
		ignitionMathCalc(rpm PASS_ENGINE_PARAMETER);
		ENGINE(m.ignitionMathTime) = GET_TIMESTAMP() - ENGINE(m.beforeIgnitionMath);
	}

	if (eventIndex == 0) {
		scheduleIgnitionAndFuelEvents(rpm, revolutionIndex PASS_ENGINE_PARAMETER);
	}

//	triggerEventsQueue.executeAll(getCrankEventCounter());

	/**
	 * For fuel we schedule start of injection based on trigger angle, and then inject for
	 * specified duration of time
	 */
	handleFuel(limitedFuel, eventIndex, rpm PASS_ENGINE_PARAMETER);
	/**
	 * For spark we schedule both start of coil charge and actual spark based on trigger angle
	 */
	handleSpark(limitedSpark, eventIndex, rpm,
			&engine->engineConfiguration2->ignitionEvents[revolutionIndex] PASS_ENGINE_PARAMETER);
#if (EFI_HISTOGRAMS && EFI_PROD_CODE) || defined(__DOXYGEN__)
	int diff = hal_lld_get_counter_value() - beforeCallback;
	if (diff > 0)
	hsAdd(&mainLoopHisto, diff);
#endif /* EFI_HISTOGRAMS */

	if (eventIndex == 0) {
		ENGINE(m.mainTriggerCallbackTime) = GET_TIMESTAMP() - ENGINE(m.beforeMainTrigger);
	}
}

#if EFI_ENGINE_SNIFFER || defined(__DOXYGEN__)
#include "engine_sniffer.h"
#endif

static void showTriggerHistogram(void) {
	printAllCallbacksHistogram();
	showMainHistogram();
#if EFI_ENGINE_SNIFFER || defined(__DOXYGEN__)
	showWaveChartHistogram();
#endif
}

void MainTriggerCallback::init(Engine *engine) {
	efiAssertVoid(engine!=NULL, "engine NULL");
	this->engine = engine;
}

static void showMainInfo(Engine *engine) {
#if EFI_PROD_CODE || defined(__DOXYGEN__)
	int rpm = engine->rpmCalculator.getRpm(PASS_ENGINE_PARAMETER_F);
	float el = getEngineLoadT(PASS_ENGINE_PARAMETER_F);
	scheduleMsg(logger, "rpm %d engine_load %f", rpm, el);
	scheduleMsg(logger, "fuel %fms timing %f", getFuelMs(rpm PASS_ENGINE_PARAMETER), engine->engineState.timingAdvance);
#endif
}

void initMainEventListener(Logging *sharedLogger, Engine *engine) {
	logger = sharedLogger;
	efiAssertVoid(engine!=NULL, "null engine");

	mainTriggerCallbackInstance.init(engine);

#if EFI_PROD_CODE || defined(__DOXYGEN__)
	addConsoleAction("performanceinfo", showTriggerHistogram);
	addConsoleActionP("maininfo", (VoidPtr) showMainInfo, engine);

	printMsg(logger, "initMainLoop: %d", currentTimeMillis());
	if (!isInjectionEnabled(mainTriggerCallbackInstance.engine->engineConfiguration))
		printMsg(logger, "!!!!!!!!!!!!!!!!!!! injection disabled");
#endif

#if EFI_HISTOGRAMS || defined(__DOXYGEN__)
	initHistogram(&mainLoopHisto, "main callback");
#endif /* EFI_HISTOGRAMS */

	addTriggerEventListener(mainTriggerCallback, "main loop", engine);
}

int isIgnitionTimingError(void) {
	return ignitionErrorDetection.sum(6) > 4;
}

#endif /* EFI_ENGINE_CONTROL */

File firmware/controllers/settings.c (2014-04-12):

/**
 * @file settings.c
 * @brief This file is about configuring engine via the human-readable protocol
 *
 * @date Dec 30, 2012
 * @author Andrey Belomutskiy, (c) 2012-2014
 */

#include "main.h"
#include "settings.h"

#include "eficonsole.h"
#include "engine_configuration.h"
#include "flash_main.h"
#include "engine_controller.h"
#include "rusefi.h"
#include "thermistors.h"
#include "adc_inputs.h"
#include "interpolation.h"
#include "tps.h"

#if EFI_PROD_CODE
#include "pin_repository.h"
#endif /* EFI_PROD_CODE */

static Logging logger;

static char LOGGING_BUFFER[1000];

extern engine_configuration_s *engineConfiguration;
extern engine_configuration2_s *engineConfiguration2;
extern board_configuration_s *boardConfiguration;

static void doPrintConfiguration(void) {
	printConfiguration(engineConfiguration, engineConfiguration2);
}

static void printIntArray(int array[], int size) {
	for (int j = 0; j < size; j++)
		print("%d ", array[j]);
	print("\r\n");
}

void printFloatArray(char *prefix, float array[], int size) {
	appendMsgPrefix(&logger);
	appendPrintf(&logger, prefix);
	for (int j = 0; j < size; j++)
		appendPrintf(&logger, "%f ", array[j]);
	appendMsgPostfix(&logger);
	scheduleLogging(&logger);
}

char* getConfigurationName(engine_configuration_s *engineConfiguration) {
	switch (engineConfiguration->engineType) {
#if EFI_SUPPORT_DODGE_NEON
	case DODGE_NEON_1995:
		return "Dodge Neon";
#endif /* EFI_SUPPORT_DODGE_NEON */
#if EFI_SUPPORT_FORD_ASPIRE
	case FORD_ASPIRE_1996:
		return "Ford Aspire";
#endif /* EFI_SUPPORT_FORD_ASPIRE */
#if EFI_SUPPORT_FORD_FIESTA
	case FORD_FIESTA:
		return "Ford Fiesta";
#endif /* EFI_SUPPORT_FORD_FIESTA */
#if EFI_SUPPORT_NISSAN_PRIMERA
	case NISSAN_PRIMERA:
		return "Nissan Primera";
#endif /* EFI_SUPPORT_NISSAN_PRIMERA */
	case HONDA_ACCORD:
		return "Honda Accord";
	case FORD_INLINE_6_1995:
		return "Ford 1995 inline 6";
	case GY6_139QMB:
		return "Gy6 139qmb";
	case MAZDA_MIATA_NB:
		return "Mazda Miata NB";
	case MAZDA_323:
		return "Mazda 323";
	case SATURN_ION_2004:
		return "Saturn Ion";
	case MINI_COOPER_R50:
		return "Mini Cooper R50";
	case FORD_ESCORT_GT:
		return "Ford Escort GT";
	default:
		return NULL;
	}
}

/**
 * @brief	Prints current engine configuration to human-readable console.
 */
void printConfiguration(engine_configuration_s *engineConfiguration, engine_configuration2_s *engineConfiguration2) {

	scheduleMsg(&logger, getConfigurationName(engineConfiguration));

	scheduleMsg(&logger, "configurationVersion=%d", getGlobalConfigurationVersion());

	for (int k = 0; k < FUEL_LOAD_COUNT; k++) {
//		print("line %d (%f): ", k, engineConfiguration->fuelKeyBins[k]);
//		for (int r = 0; r < FUEL_RPM_COUNT; r++) {
//			print("%f ", engineConfiguration->fuelTable[k][r]);
//		}
//		print("\r\n");
	}

	printFloatArray("RPM bin: ", engineConfiguration->fuelRpmBins, FUEL_RPM_COUNT);

	printFloatArray("Y bin: ", engineConfiguration->fuelLoadBins, FUEL_LOAD_COUNT);

	printFloatArray("CLT: ", engineConfiguration->cltFuelCorr, CLT_CURVE_SIZE);
	printFloatArray("CLT bins: ", engineConfiguration->cltFuelCorrBins, CLT_CURVE_SIZE);

	printFloatArray("IAT: ", engineConfiguration->iatFuelCorr, IAT_CURVE_SIZE);
	printFloatArray("IAT bins: ", engineConfiguration->iatFuelCorrBins, IAT_CURVE_SIZE);

	printFloatArray("vBatt: ", engineConfiguration->battInjectorLagCorr, VBAT_INJECTOR_CURVE_SIZE);
	printFloatArray("vBatt bins: ", engineConfiguration->battInjectorLagCorrBins, VBAT_INJECTOR_CURVE_SIZE);

//	appendMsgPrefix(&logger);

	scheduleMsg(&logger, "rpmHardLimit: %d", engineConfiguration->rpmHardLimit);
	scheduleMsg(&logger, "rpmMultiplier=%f", engineConfiguration->rpmMultiplier);

	scheduleMsg(&logger, "tpsMin: %d", engineConfiguration->tpsMin);
	scheduleMsg(&logger, "tpsMax: %d", engineConfiguration->tpsMax);

	scheduleMsg(&logger, "timingMode: %d", engineConfiguration->timingMode);
	scheduleMsg(&logger, "fixedModeTiming: %d", (int) engineConfiguration->fixedModeTiming);
	scheduleMsg(&logger, "ignitionOffset=%f", engineConfiguration->ignitionOffset);
	scheduleMsg(&logger, "injectionOffset=%f", engineConfiguration->injectionOffset);

	scheduleMsg(&logger, "crankingChargeAngle=%f", engineConfiguration->crankingChargeAngle);
	scheduleMsg(&logger, "crankingTimingAngle=%f", engineConfiguration->crankingTimingAngle);
	scheduleMsg(&logger, "globalTriggerAngleOffset=%f", engineConfiguration->globalTriggerAngleOffset);

//	scheduleMsg(&logger, "analogChartMode: %d", engineConfiguration->analogChartMode);
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

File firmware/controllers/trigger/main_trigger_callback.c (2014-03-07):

/**
 * @file    main_trigger_callback.c
 * @brief   Main logic is here!
 *
 * See http://rusefi.com/docs/html/
 *
 * @date Feb 7, 2013
 * @author Andrey Belomutskiy, (c) 2012-2014
 */

#include "main.h"
#include "main_trigger_callback.h"

#include "trigger_central.h"
#include "rpm_calculator.h"
#include "signal_executor.h"
#include "eficonsole.h"
#include "engine_math.h"

#include "engine_configuration.h"
#include "interpolation.h"
#include "advance_map.h"
#include "allsensors.h"
#include "cyclic_buffer.h"
#include "histogram.h"
#include "fuel_math.h"
#include "histogram.h"
#include "rfiutil.h"

// todo: move this to engine_configuration2_s for now

extern engine_configuration_s *engineConfiguration;
extern engine_configuration2_s *engineConfiguration2;

static cyclic_buffer ignitionErrorDetection;

static Logging logger;
int isInjectionEnabled(void);

/**
 * this field is accessed only from shaft sensor event handler.
 * This is not a method variable just to save us from stack overflow.
 */
static ActuatorEventList events;

static void handleFuelInjectionEvent(ActuatorEvent *event, int rpm) {
//	int cylinderId = event->actuatorId;
//	if (cylinderId == 0)
//		return; // no cylinder should be fired at this event
//	assertCylinderId(cylinderId, "onShaftSignal");

	if (rpm > engineConfiguration->rpmHardLimit) {
		scheduleSimpleMsg(&logger, "RPM above hard limit ", rpm);
		return;
	}

	int fuelTicks = (int) (getFuelMs(rpm) * engineConfiguration->globalFuelCorrection * TICKS_IN_MS);
	if (fuelTicks < 0) {
		scheduleSimpleMsg(&logger, "ERROR: negative injectionPeriod ", fuelTicks);
		return;
	}

	int delay = (int) (getOneDegreeTime(rpm) * event->angleOffset);

	if (isCranking())
		scheduleSimpleMsg(&logger, "crankingFuel=", fuelTicks);

	scheduleOutput(event->actuator, delay, fuelTicks, chTimeNow());
}

static void handleFuel(ShaftEvents ckpSignalType, int eventIndex) {
	if (!isInjectionEnabled())
		return;
	chDbgCheck(eventIndex < engineConfiguration2->triggerShape.shaftPositionEventCount, "event index");

	ActuatorEventList *source =
			isCranking() ?
					&engineConfiguration2->engineEventConfiguration.crankingInjectionEvents :
					&engineConfiguration2->engineEventConfiguration.injectionEvents;
	findEvents(eventIndex, source, &events);

	if (events.size == 0)
		return;

//	scheduleSimpleMsg(&logger, "eventId size=", events.size);

	int rpm = getRpm();

	for (int i = 0; i < events.size; i++) {
		ActuatorEvent *event = &events.events[i];
		handleFuelInjectionEvent(event, rpm);
	}
}

static void handleSparkEvent(ActuatorEvent *event, int rpm) {
	if (rpm == 0)
		return;
	float advance = getAdvance(rpm, getEngineLoad());

	float sparkAdvanceMs = getOneDegreeTimeMs(rpm) * advance;

	float dwellMs = getSparkDwellMs(rpm);
	if (dwellMs < 0)
		firmwareError("invalid dwell: %f at %d", dwellMs, rpm);

	if (dwellMs <= 0)
		return; // hard RPM limit was hit

	float sparkDelay = (int) (getOneDegreeTimeMs(rpm) * event->angleOffset + sparkAdvanceMs - dwellMs);
	int isIgnitionError = sparkDelay < 0;
	cbAdd(&ignitionErrorDetection, isIgnitionError);
	if (isIgnitionError) {
		scheduleMsg(&logger, "Negative spark delay=%f", sparkDelay);
		sparkDelay = 0;
		//return;
	}

	scheduleOutput(event->actuator, sparkDelay * TICKS_IN_MS, dwellMs * TICKS_IN_MS, chTimeNow());
}

static void handleSpark(ShaftEvents ckpSignalType, int eventIndex) {
	int rpm = getRpm();

	findEvents(eventIndex, &engineConfiguration2->engineEventConfiguration.ignitionEvents, &events);
	if (events.size == 0)
		return;

//	scheduleSimpleMsg(&logger, "eventId spark ", eventIndex);

	for (int i = 0; i < events.size; i++) {
		ActuatorEvent *event = &events.events[i];
		handleSparkEvent(event, rpm);
	}
}

static histogram_s mainLoopHisto;

void showMainHistogram(void) {
	printHistogram(&logger, &mainLoopHisto);
}

/**
 * This is the main entry point into the primary shaft signal handler signal. Both injection and ignition are controlled from this method.
 */
static void onShaftSignal(ShaftEvents ckpSignalType, int eventIndex) {
	chDbgCheck(eventIndex < engineConfiguration2->triggerShape.shaftPositionEventCount, "event index");
	int beforeCallback = hal_lld_get_counter_value();
	handleFuel(ckpSignalType, eventIndex);
	handleSpark(ckpSignalType, eventIndex);
	int diff = hal_lld_get_counter_value() - beforeCallback;
	if (diff > 0)
		hsAdd(&mainLoopHisto, diff);
}

static void showTriggerHistogram(void) {
	printAllCallbacksHistogram();
	showMainHistogram();
}

void initMainEventListener() {
	addConsoleAction("trigger_hist", showTriggerHistogram);

	initLogging(&logger, "main event handler");
	printMsg(&logger, "initMainLoop: %d", chTimeNow());
	cbInit(&ignitionErrorDetection);
	resetHistogram(&mainLoopHisto, "main");

	if (!isInjectionEnabled())
		printMsg(&logger, "!!!!!!!!!!!!!!!!!!! injection disabled");

	registerShaftPositionListener(&onShaftSignal, "main loop");
}

int isIgnitionTimingError(void) {
	return cbSum(&ignitionErrorDetection, 6) > 4;
}

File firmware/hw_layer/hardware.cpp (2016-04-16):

/**
 * @file    hardware.cpp
 * @brief   Hardware package entry point
 *
 * @date May 27, 2013
 * @author Andrey Belomutskiy, (c) 2012-2016
 */

#include "main.h"
#include "adc_inputs.h"
#include "can_hw.h"
#include "console_io.h"
#include "hardware.h"
#include "io_pins.h"
#include "pin_repository.h"
#include "rtc_helper.h"
#include "rfiutil.h"
#include "injector_central.h"
#include "vehicle_speed.h"

#include "trigger_input.h"
#include "eficonsole.h"
#include "max31855.h"

#if EFI_PROD_CODE
#include "AdcConfiguration.h"
#include "board_test.h"
#include "mcp3208.h"
#include "HIP9011.h"
#include "histogram.h"
#include "mmc_card.h"
#include "neo6m.h"
#include "lcd_HD44780.h"
#include "settings.h"
#include "algo.h"
#include "joystick.h"
#include "trigger_central.h"
#include "svnversion.h"
#include "engine_configuration.h"
#include "wbo.h"
#endif

#if EFI_SPEED_DENSITY
#include "map_averaging.h"
#endif /* EFI_SPEED_DENSITY */

#if EFI_INTERNAL_FLASH
#include "flash_main.h"
#endif /* EFI_INTERNAL_FLASH */

EXTERN_ENGINE
;
extern bool hasFirmwareErrorFlag;

static Mutex spiMtx;

int maxNesting = 0;

#if HAL_USE_SPI || defined(__DOXYGEN__)
static bool isSpiInitialized[5] = { false, false, false, false, false };

/**
 * Only one consumer can use SPI bus at a given time
 */
void lockSpi(spi_device_e device) {
	efiAssertVoid(getRemainingStack(chThdSelf()) > 128, "lockSpi");
	// todo: different locks for different SPI devices!
	chMtxLock(&spiMtx);
}

void unlockSpi(void) {
	chMtxUnlock();
}

static void initSpiModules(board_configuration_s *boardConfiguration) {
	if (boardConfiguration->is_enabled_spi_2) {
		turnOnSpi(SPI_DEVICE_2);
	}
	if (boardConfiguration->is_enabled_spi_3) {
		turnOnSpi(SPI_DEVICE_3);
	}
}

SPIDriver * getSpiDevice(spi_device_e spiDevice) {
	if (spiDevice == SPI_NONE) {
		return NULL;
	}
#if STM32_SPI_USE_SPI1 || defined(__DOXYGEN__)
	if (spiDevice == SPI_DEVICE_1) {
		return &SPID1;
	}
#endif
#if STM32_SPI_USE_SPI2 || defined(__DOXYGEN__)
	if (spiDevice == SPI_DEVICE_2) {
		return &SPID2;
	}
#endif
#if STM32_SPI_USE_SPI3 || defined(__DOXYGEN__)
	if (spiDevice == SPI_DEVICE_3) {
		return &SPID3;
	}
#endif
	firmwareError("Unexpected SPI device: %d", spiDevice);
	return NULL;
}
#endif

#if HAL_USE_I2C || defined(__DOXYGEN__)
static I2CConfig i2cfg = { OPMODE_I2C, 100000, STD_DUTY_CYCLE, };

void initI2Cmodule(void) {
	print("Starting I2C module\r\n");
	i2cInit();
	i2cStart(&I2CD1, &i2cfg);

	mySetPadMode("I2C clock", EFI_I2C_SCL_PORT, EFI_I2C_SCL_PIN,
	PAL_MODE_ALTERNATE(EFI_I2C_AF) | PAL_STM32_OTYPE_OPENDRAIN);
	mySetPadMode("I2C data", EFI_I2C_SDA_PORT, EFI_I2C_SDA_PIN,
	PAL_MODE_ALTERNATE(EFI_I2C_AF) | PAL_STM32_OTYPE_OPENDRAIN);
}

//static char txbuf[1];

static void sendI2Cbyte(int addr, int data) {
//	i2cAcquireBus(&I2CD1);
//	txbuf[0] = data;
//	i2cMasterTransmit(&I2CD1, addr, txbuf, 1, NULL, 0);
//	i2cReleaseBus(&I2CD1);
}

#endif

static Logging *sharedLogger;

#if EFI_PROD_CODE

extern AdcDevice fastAdc;

#define TPS_IS_SLOW -1

static int fastMapSampleIndex;
static int hipSampleIndex;
static int tpsSampleIndex;

extern int tpsFastAdc;

/**
 * This method is not in the adc* lower-level file because it is more business logic then hardware.
 */
void adc_callback_fast(ADCDriver *adcp, adcsample_t *buffer, size_t n) {
	efiAssertVoid(getRemainingStack(chThdSelf()) > 64, "lowstck12a");

	(void) buffer;
	(void) n;
	/**
	 * Note, only in the ADC_COMPLETE state because the ADC driver fires an
	 * intermediate callback when the buffer is half full.
	 * */
	if (adcp->state == ADC_COMPLETE) {
		/**
		 * this callback is executed 10 000 times a second, it needs to be as fast as possible
		 */
		efiAssertVoid(getRemainingStack(chThdSelf()) > 128, "lowstck#9b");

#if EFI_MAP_AVERAGING
		mapAveragingCallback(fastAdc.samples[fastMapSampleIndex]);
#endif /* EFI_MAP_AVERAGING */
#if EFI_HIP_9011 || defined(__DOXYGEN__)
		if (boardConfiguration->isHip9011Enabled) {
			hipAdcCallback(fastAdc.samples[hipSampleIndex]);
		}
#endif
		if (tpsSampleIndex != TPS_IS_SLOW) {
//			tpsFastAdc = fastAdc.samples[tpsSampleIndex];
		}
	}
}

static void calcFastAdcIndexes(void) {
	fastMapSampleIndex = fastAdc.internalAdcIndexByHardwareIndex[engineConfiguration->map.sensor.hwChannel];
	hipSampleIndex =
			engineConfiguration->hipOutputChannel == EFI_ADC_NONE ?
					-1 : fastAdc.internalAdcIndexByHardwareIndex[engineConfiguration->hipOutputChannel];
	if (engineConfiguration->tpsAdcChannel != EFI_ADC_NONE) {
		tpsSampleIndex = fastAdc.internalAdcIndexByHardwareIndex[engineConfiguration->tpsAdcChannel];
	} else {
		tpsSampleIndex = TPS_IS_SLOW;
	}
}

static void adcConfigListener(Engine *engine) {
	calcFastAdcIndexes();
}

void turnOnHardware(Logging *sharedLogger) {
#if EFI_SHAFT_POSITION_INPUT || defined(__DOXYGEN__)
	turnOnTriggerInputPins(sharedLogger);
#endif /* EFI_SHAFT_POSITION_INPUT */
}

void applyNewHardwareSettings(void) {
#if EFI_SHAFT_POSITION_INPUT || defined(__DOXYGEN__)
	applyNewTriggerInputPins();
#endif /* EFI_SHAFT_POSITION_INPUT */
	stopInjectionPins();
	stopIgnitionPins();

	startInjectionPins();
	startIgnitionPins();
}
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

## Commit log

2015-06-22 60/2 VW
    [rusefi_config.txt]
2015-06-22 better name
    [rusefi_config.txt]
2015-06-26 tiny progress
    [rusefi_config.txt]
2015-06-26 'disbaled' option for ADC properties
    [rusefi_config.txt]
2015-06-26 AFR refactoring
    [rusefi_config.txt]
2015-06-26 accord trigger
    [rusefi_config.txt]
2015-07-03 hip mode
    [rusefi_config.txt]
2015-07-05 new board
2015-07-08 old board info
2015-07-11 SPI progress
2015-07-13 hip SPI fix
2015-07-13 HIP progress
    [DD_HIP9011.sch, Misc_Vias.sch, PWR_buck_12V_switcher.sch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]
2015-07-13 hip flexibility
    [rusefi_config.txt]
2015-07-27 filling 8606<>8624 gap
    [MAIN_rfi_report_2015-07-16 08_00.csv]
2015-08-30 MAP range validation
    [rusefi_config.txt]
2015-08-30 pin coflict with debugger
2015-08-30 multi-threading bug: dead serial port was blocking AWT thread
2015-08-31 use only first trigger
    [rusefi_config.txt]
2015-09-06 https://sourceforge.net/p/rusefi/tickets/224/ BUGFIX - pretty minor issue
    [main_trigger_callback.cpp]
2015-09-07 measuring MAP for each cylinder
2015-09-10 3 cylinder support
2015-09-12 daihatsu fix
    [rusefi_config.txt]
2015-09-12 CJ125 symbol
    [O2_input_CJ125.sch]
2015-09-12 acceleration graph
    [rusefi_config.txt]
2015-09-13 reducing memory footprint
2015-09-16 turn on/off LCD screen
    [rusefi_config.txt]
2015-09-25 auto-showing gap in case of error
2015-10-05 fresh version
    [PWR_5V_linear.kicad_pcb, PWR_5V_linear.sch, PWR_5V_linear_by-ref.csv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]
2015-10-05 power supply changes
    [DD_HIP9011.sch, Misc_Vias.sch, PWR_buck_12V_switcher.sch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]
2015-10-12 pa2&pa3 as digital input
    [rusefi_config.txt]
2015-10-18 idle position gauge & refactoring
    [rusefi_config.txt]
2015-10-20 2nd idle implementation & better field name
    [rusefi_config.txt]
2015-10-20 injection phase range fix
    [rusefi_config.txt]
2015-11-05 IAT correction bug, was CLT-based correction
    [rusefi.cpp]
2015-11-12 better field name
    [rusefi_config.txt]
2015-11-12 maybe a bugfix - FATAL error in case of set_engine_type timing
2015-12-11 ts file version fix & typo fix
    [rusefi_config.txt]
2015-12-22 removing unused field
    [rusefi_config.txt]
2015-12-25 idle valve bench UI
2015-12-25 idle valve bench
2015-12-25 idle diode
2015-12-27 current config
2015-12-28 main relay
2015-12-28 rover K
    [rusefi_config.txt]
2015-12-31 refactoring & breaking code
    [rusefi_config.txt]
2015-12-31 decel stuff
    [rusefi_config.txt]
2016-01-03 better sensor naming
2016-01-03 making progress
    [rusefi_config.txt]
2016-01-05 at least it did not die
2016-01-08 better manual fuel pump control
2016-01-08 fixing dodge MAP calibration
2016-01-08 newer version
    [ion.kicad_pcb, ion.sch]
2016-01-09 kicad 4
    [DD_HIP9011.sch, Misc_Vias.sch, PWR_buck_12V_switcher.sch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]
2016-01-15 refactoring: eliminating engineCycleDuration, operationMode should be enough
    [rusefi_config.txt]
2016-01-16 #250 two wire wasted spark
2016-01-21 reducing ADC error - averaging with 8 samples
2016-01-21 PID improvements - moving towards online configuration
2016-01-21 0.4 version
    [PWR_buck_12V_switcher.kicad_pcb, PWR_buck_12V_switcher.sch]
2016-01-21 VBatt filter
2016-01-22 making output area larger
    [rusefi_config.txt]
2016-01-23 mock voltage into real hardware
2016-01-23 mock voltage for real firmware
2016-01-24 more alternator pid debugging
2016-01-25 reducing coupling
2016-01-25 reducing code duplication & memory footprint
2016-01-25 #192 BUG spark/fuel scheduling jitter
    [engine_configuration.cpp, main_trigger_callback.cpp]
2016-01-25 one step backwards - fixing build
    [main_trigger_callback.cpp]
2016-01-28 error message fix, default 626 config fix
    [rusefi.cpp]
2016-01-28 #260 engine and sensor sniffer dynamic limit
    [rusefi_config.txt]
2016-01-30 #261 Low-pass_filter for slow ADC sensors
    [rusefi_config.txt]
2016-01-31 ADC & TPS progress
2016-02-01 filtered slow ADC TPS
2016-02-05 #262 configuration setting to disable text protocol
    [rusefi_config.txt]
2016-02-05 actual bugfix
    [rusefi_config.txt]
2016-02-05 PID offset refactoring
    [rusefi_config.txt]
2016-02-05 #263 PID-based target AFR warmup control
    [rusefi_config.txt]
2016-02-06 improving PID class
2016-02-06 #263 PID-based target AFR warmup control & docs/refactoring
2016-02-06 PID refactoring
2016-02-09 extra precision
    [rusefi_config.txt]
2016-02-14 work-around for TS float curve issue
    [engine_configuration.cpp]
2016-02-27 current settings
2016-02-27 #273 rusefi.ini usability issues
    [rusefi_config.txt]
2016-02-28 on/off alternator
    [rusefi_config.txt]
2016-02-28 #272 boost cut
    [rusefi_config.txt]
2016-03-02 VR board
    [vrs_io_1.kicad_pcb, vrs_io_1.sch]
2016-03-04 #127 FSIO: add user-defined maps
    [rusefi_config.txt]
2016-03-07 BOM for VR board
    [vrs_io_1.csv, vrs_io_1.sch, vrs_io_1_by-ref.csv]
2016-03-08 v_batt calibration
2016-03-09 acceleration enrichment
    [rusefi_config.txt]
2016-03-12 map acceleration taper
    [rusefi_config.txt]
2016-03-20 new dialog "tuning"->"console monitoring"
    [rusefi_config.txt]
2016-03-21 starter relay
2016-03-22 bugfix with debugMode
    [rusefi_config.txt]
2016-04-10 moving to 4.0
    [DD_HIP9011.sch, Misc_Vias.sch, PWR_buck_12V_switcher.sch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]
2016-04-12 #281 better FATAL error handling
    [rusefi.cpp]
2016-04-16 BUGFIX - debug version would not start on erased chip
    [hardware.cpp, rusefi.cpp]
2016-04-23 correcting pin comments

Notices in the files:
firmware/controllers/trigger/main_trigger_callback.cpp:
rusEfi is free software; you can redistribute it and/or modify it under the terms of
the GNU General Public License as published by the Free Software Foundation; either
